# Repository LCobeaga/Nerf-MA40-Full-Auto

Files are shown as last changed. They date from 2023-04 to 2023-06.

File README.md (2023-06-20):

# Nerf-MA40-Full-Auto

This file set is an almost drop in replacemnt for the semi automatic pusher to convert the Nerf MA40 into a full auto firing blaster. 

Note that the hardware is all flycore except the pusher bolt, which is designed for an M2 instead of an M3 to give the pusher the maximum possible throw.

## Hardware

(3) M2.6x10mm toy screws (if not using a pusher return sensor, only 1)

(2) M2.6x12mm toy screws

(1) M2x6mm socket head bolt

(1) M2 nut

(1) N20 Motor (1000 rpm or below, higher rpm motors have insuffiucent torque and burn out)

(1) Cherry DB2 style switch (for pusher return sensor)

(1) Omron/Tezuo style microswitch 

## Wiring

Its set up just like a flycore blaster so just wire the same way. 

I've included the PDF assembly guide of a QUIK so decide which wiring option you prefer and do that.

## 3D Printing

I found these orientations work best, a little support is needed on the pusher and motor mount.

print orientation

I also suggest printing the post in the center of the disk solid for extra support on the D-slot.

## Blaster Modificatons 

There are some tabs and walls needed to be cut for the pusher and cables to fit.

In the photos you will notice the pivot post is removed but that is not necessary.
If you leave the post the entire mod can be undone and retuned to semi auto if you ever decide to go back.

Wire clearance

Create a little channel for the wires to pass under the barrel near the front of the flywheels and remove the tiny spoke under the switch plate.

Right shell wall removal

Remove the walls shown, the rough cut is just clearance for the wires.

left shell

Remove the support walls shown, the top most one should be cut flush to the horizontal wall to allow for pusher clearance.

## Assembly

trigger switch

The trigger switch sits on the switch plate and is friction fit around the post and X support under it. 

motor and screw

Slot the N20 motor into the top of the motor mount and attach the switch plate in the back with a toy screw, this will also lock the motor in place.

disk assembly

screw the M2 bolt into the top flat side of the disk, and push the D slot hole onto the motor. This is a friction fit.

block placement

The pusher mechanism is friction fit between the post and wall of the mag release.
Make sure that the corner of the motor mount (red arrow) is not sitting on top of the mag release but is pushed down past it. 

pusher step 1

To insert the actual pusher first move the screw to the front of the pusher mechanism and align the pusher slot.

pusher step 2

Then place the bolt into the pusher slot.

pusher step 3

finally snap the long tab of the pusher into the old pusher channel. 

## Troubleshooting/Suggestions

If the pusher is sticking add lubriucant to the top of the pusher disk, the right side of the pusher arm, and inside both slots on the top of the pusher.

Drilling vent holes along the barrel should improve performance, which normally is hindered by the long barrel.

The OFP cage available for the MA40 seems to be off center to the right of the blaster (too low on the posts) so I've had to add about 2mm worth of M2 washers.

Before closing up the blaster make sure to add in the black cosmetic pieces at the stock and cheek rest as the wires dent to get in the way so youll have to move them around screw posts.

The wires to the pusher should be packed above the old pusher channel, and make sure the pusher has clearance for when it is in the furthest back position.

The pusher motor should turn into the shell on the return to prevent the pusher from catching on the internal ribs, i.e. clockwise looking from the top.

If the pusher works fine while the blaster is open but seems to work slowly or wont work when closed, try shaving a little material from this area of the pusher.

shave pusher spot

And thats all, have fun using your slightly more game accurate MA40 (in game the RPM is 720 so decide on your N20 motor accordingly).

<br />This work is licensed under a <a rel="license" href="http://creativecommons.org/licenses/by-nc-sa/3.0/">Creative Commons Attribution-NonCommercial-ShareAlike 3.0 Unported License</a>.

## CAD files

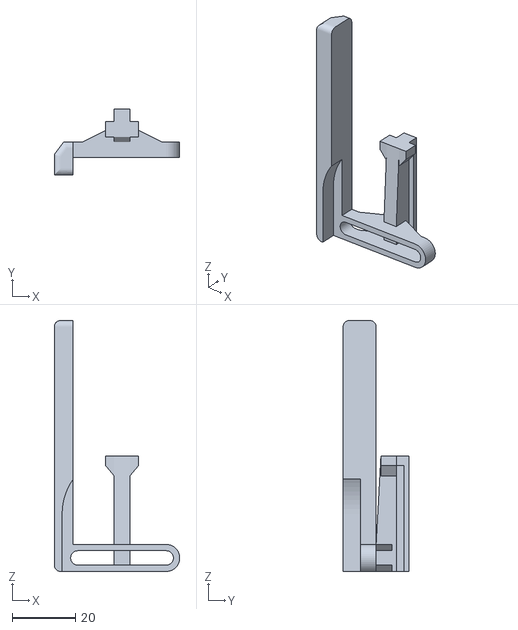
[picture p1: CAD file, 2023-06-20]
stl files/pusher.stl
39.8 x 20.9 x 79.6

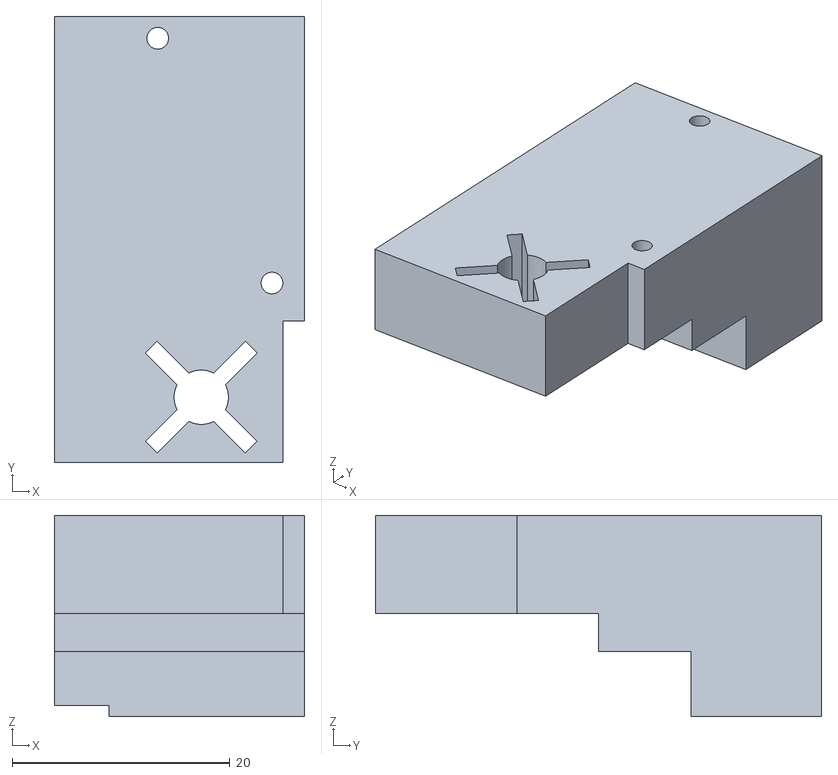
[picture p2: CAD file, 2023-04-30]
stl files/Trigger Switch Plate.stl
23.0 x 41.0 x 18.5

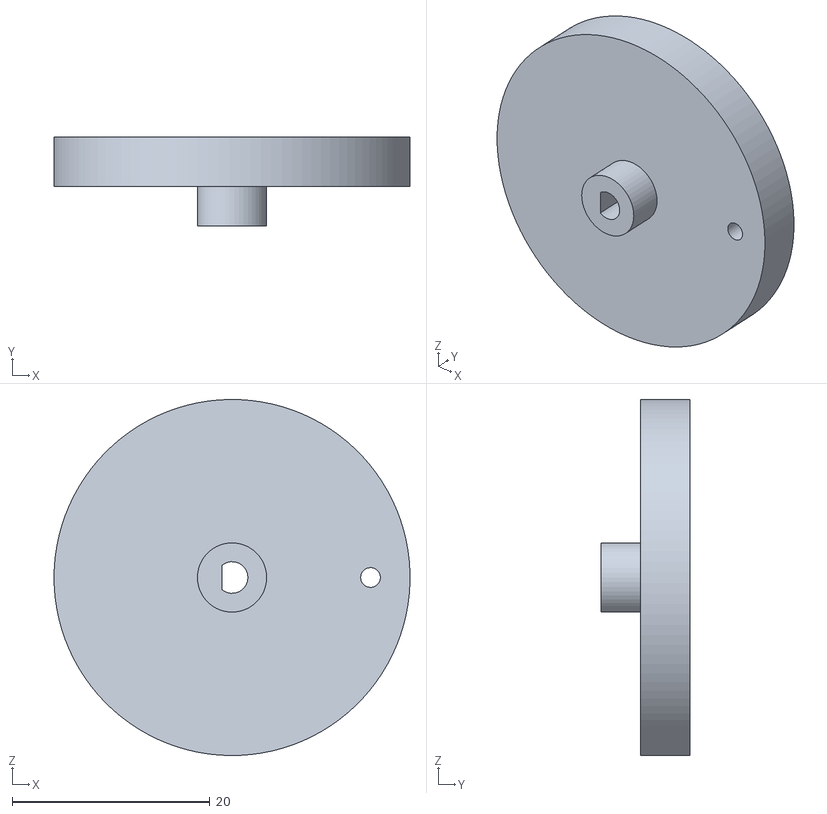
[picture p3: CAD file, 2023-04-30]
stl files/disk.stl
36.0 x 9.00 x 36.0

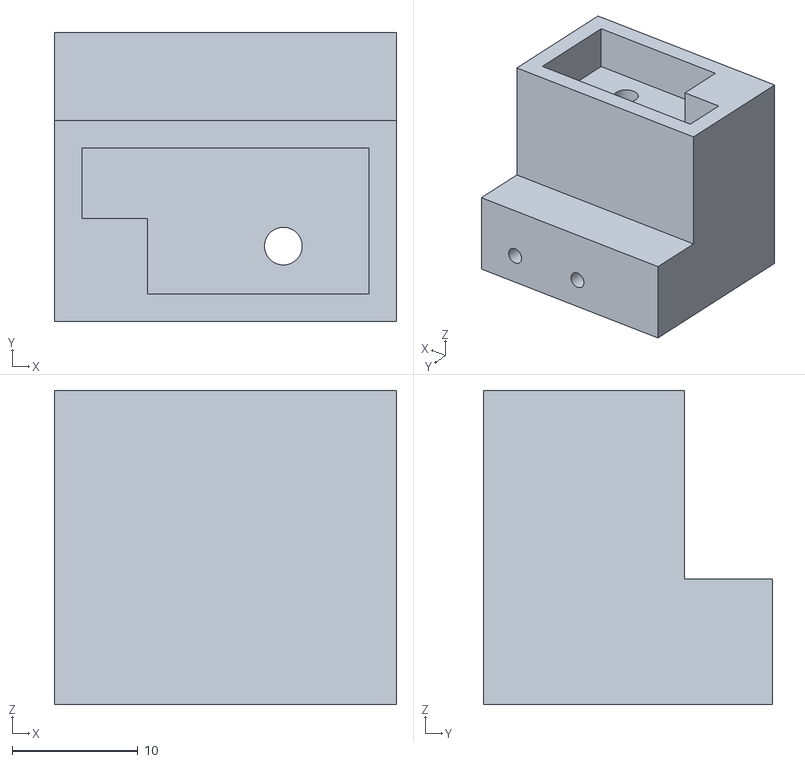
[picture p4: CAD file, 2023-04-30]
stl files/pusher return switch block.stl
27.2 x 23.0 x 25.0

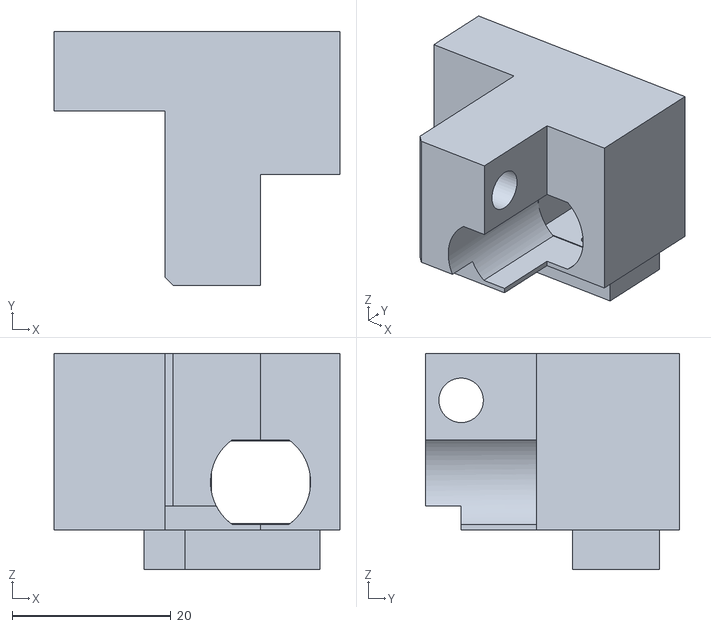
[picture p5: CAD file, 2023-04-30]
stl files/motor mount.stl
36.0 x 32.0 x 27.2
